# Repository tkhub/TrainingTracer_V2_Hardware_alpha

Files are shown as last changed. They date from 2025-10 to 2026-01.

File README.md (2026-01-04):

[TraningTracer Ver.2](https://rt-net.jp/products/traning-tracer2/)
の勝手改造版です。
tracer

## 改造・改良箇所
* 改造箇所
  * 一般的な3端子レギュレータの端子配置(Vin-GND-Vout)への対応
    * [スーパー3端子レギュレータ](https://akizukidenshi.com/catalog/g/g107178/)が使用でき、高電圧なLiPoバッテリーに対応可能
  * 逆電圧による3端子レギュレータ破壊防止のDiを追加
  * 改造用に各種電源とI2Cのピンアウトを設定
  * ディスコンになったBMX055のかわりにBNO055を搭載可能
    * ショートピンの設定(ハンダ盛り)が必要
  * 自励式ブザーの代わりに圧電スピーカーを搭載可能でより多彩な情報を通知可能
    * 自励式ブザーを使用時は直流阻止コンデンサのC5をショートすること
  * I2Cディスプレイ用コネクタの設定
    * [0.96インチOLEDディスプレイ](https://akizukidenshi.com/catalog/g/g112031/)のような追加ディスプレイによりより多くの情報をユーザーに通知可能
  * 基板上にラインズレ量を測るスケールを追加
  * その他小変更
* 改良箇所
  * パイロットランプの追加
    * 電源入れっぱなしの防止
  * [バッテリー電圧計測のブレ対策にコンデンサC4を追加](https://github.com/rt-net/TrainingTracer_V2_Hardware/issues/1)
  * [回路図上のラベルとセンサの物理配置、ソフトの命名の整合性確保](https://github.com/rt-net/TrainingTracer_V2_Hardware/issues/2)
  * [プログラム書き込み中にモータが回転する問題の解決](https://github.com/rt-net/TrainingTracer_Hardware/issues/7)

## フォルダ構成

* 3d_cad_data
　トレーニングトレーサーの3DCADデータ
  STPファイルとIGSファイルで保存しています。
* 3d_print_parts
　トレーニングトレーサーの3Dプリント部品のデータ
  * TrainingTracer_Motor_Mount.stl
    トレーニングトレーサーのモータマウントの3Dモデルです。
  * TrainingTracerV2_Slider.stl
    トレーニングトレーサーのスライダーの3Dモデルです。
  * TrainingTracerV2_Wheel.stl
    トレーニングトレーサーのホイールの3Dモデルです。
* circuits
　トレーニングトレーサーの回路図とNucleoの追加工マニュアル
  * TrainingTracer
    * KiCadのプロジェクトフォルダ
  * old
    * TrainingTracerV2_circuit_rev1.0.pdf
    トレーニングトレーサーのメイン基板の回路図です。
    * TrainingTracer_marker_circuit.pdf
    トレーニングトレーサーのマーカーセンサ基板の回路図です。
  * TrainingTracer_PCB.pdf
    改造後の基板
  * TrainingTracer_SCH.pdf
    改造後の回路図
  * 出荷時のNucleoの追加工.pdf
    トレーニングトレーサーのNucleoボードに行った追加工の情報です。
    
## 開発について

本リポジトリはオープンソースですが、開発はオープンではありません。  
機能追加については社内のガイドラインを優先します。  
誤植や不具合の修正は常時受け付けています。詳しくは[コントリビューションガイドライン](https://github.com/rt-net/.github/blob/master/CONTRIBUTING.md)に従ってください。

## ライセンス

(C) 2020 RT Corporation \<support@rt-net.jp\>

各ファイルはライセンスがファイル中に明記されている場合、そのライセンスに従います。特に明記されていない場合は、Apache License, Version 2.0に基づき公開されています。  
ライセンスの全文は[LICENSE](./LICENSE)または[https://www.apache.org/licenses/LICENSE-2.0](https://www.apache.org/licenses/LICENSE-2.0)から確認できます。

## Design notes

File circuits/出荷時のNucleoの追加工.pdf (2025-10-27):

© 2020

# トレーニングトレーサーにおける

# Nucleoの追加工

# 本資料について

トレーニングトレーサーへNucleoを搭載するために実施した作業内容を記載していま す。別途Nucleoを購入して搭載したい場合に参照してください。

# 抵抗の加工

安全性と使いやすさを考慮して、単4アルカリ電池直列4個接続で稼働できるよう、 Nucleoに搭載の3.3Vのレギュレータを使わず、外付けのレギュータでマイコン等へ電力を 供給しています。そのため、SB14の0Ω抵抗を外す必要があります。 3.3Vを外部から入れるとST-LINKと繋がっているNRSTがずっとLOWと認識してしまい、 マイコンが起動しないので、SB9も外す必要があります。 また、アナログピンA5、A4がデータピンD5、D4に接続している状態であり、A/DとI2C が同時に使えないため、0Ω抵抗のSB16とSB18を外す必要があります。

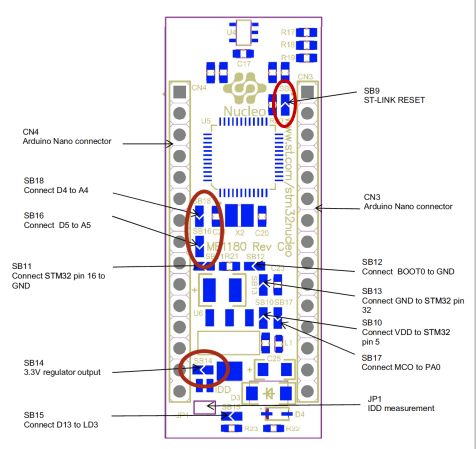
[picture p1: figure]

図.1 Nucleoボードの裏側¹

# マーカセンサについて

Nucleoのパッケージのバージョンが1.8の場合、マーカーセンサに関しては、接続されて いるピンではArduino IDEの関数がそのままでは使えないため、STEP5で機能を追加してあ ります。(パッケージのバージョンが1.9の場合は変更の必要はありません。)また、一部 Nucleoのパッケージを書き換える必要があります。NUCLEO-F303のオリジナルは、A4と D4、A5とD5がボード上で短絡しています。その関係で、A4とA5のピンに関しては、アナ ログ入力で変換できないようにパッケージ側でコメントアウトされています。プログラムを 実行する前に、テキストエディタなどでパッケージ内にある以下のファイルを修正する必要 があります。

## Windowsの場合

C:\Users\ユーザー名\ドキュメント
\ArduinoData\packages\STM32\hardware\stm32\1.8.0\variants\NUCLEO_F303K8/Pe ripheralPins.cの49と50行目のコメントアウト//を解除

## Macの場合

User/ユーザー名
/Library/Arduino15/packages/STM32/hardware/stm32/1.8.0/variants/NUCLEO_F303 K8/PeripheralPins.cの49と50行目のコメントアウト//を解除

## Linuxの場合

/home/ユーザー名
/.arduino15/packages/STM32/hardware/stm32/1.8.0/variants/NUCLEO_F303K8/Peri pheralPins.cの49と50行目のコメントアウト//を解除

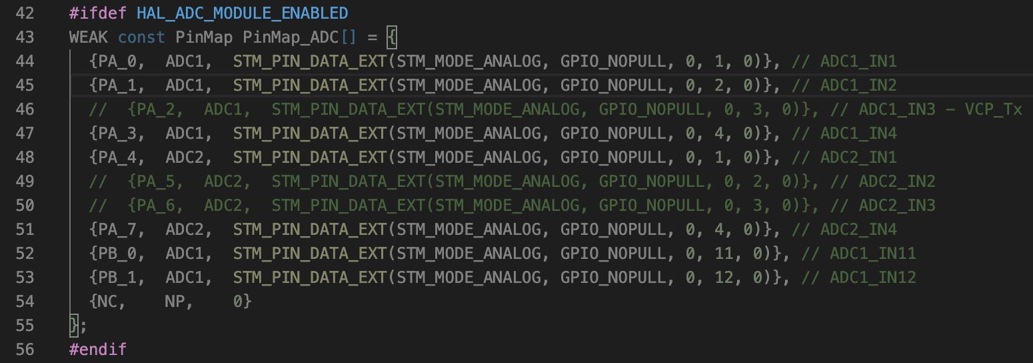
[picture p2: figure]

図.2 修正前のPeripheralPins.c

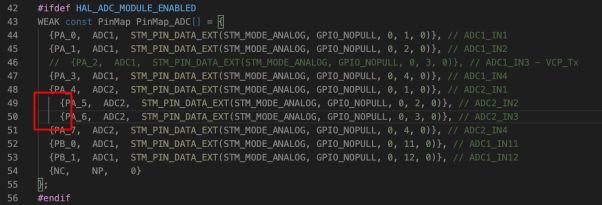
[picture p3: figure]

図.3 修正後のPeripheralPins.c

出典

1. STmicroerectronics社UM1727 User manual Getting started with STM32 Nucleo board software development tools https://www.st.com/resource/en/user_manual/dm00231744-stm32-nucleo32-boardsmb1180-stmicroelectronics.pdf (https://www.st.com/resource/en/user_manual/dm00231744-stm32-nucleo32-boards-mb1180-stmicroelectronics.pdf)

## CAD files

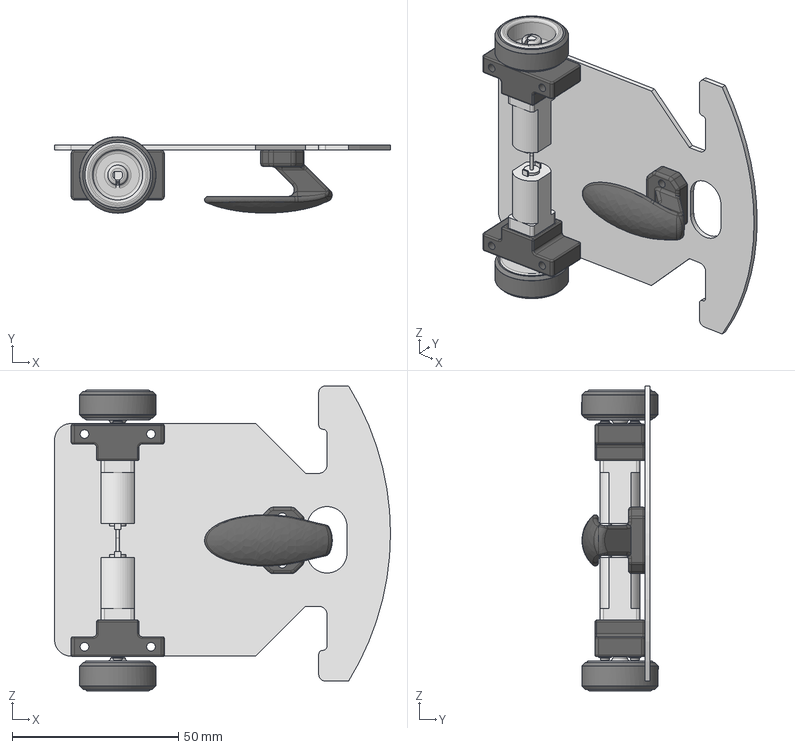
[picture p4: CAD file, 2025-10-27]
3d_cad_data/TrainingTracerV2.step
101.1 x 23.0 x 91.8 mm
MicroMetalGearmotor x 2
TrainingTracerBoard0.1
TrainingTracer_MotorMount_20200427 x 2
M1.6平ワッシャ_FW-1638-03N x 4
小ねじM1.6-4_U-1640-03 x 4
タイヤ(MZW2-20) x 2
TrainingTracer_Slider_20200420

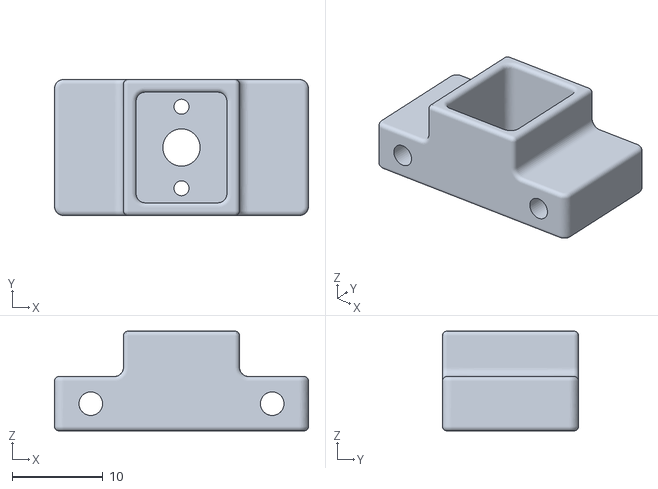
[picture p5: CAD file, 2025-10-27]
3d_print_parts/TrainingTracer_MotorMount.stl
28.0 x 15.0 x 11.0

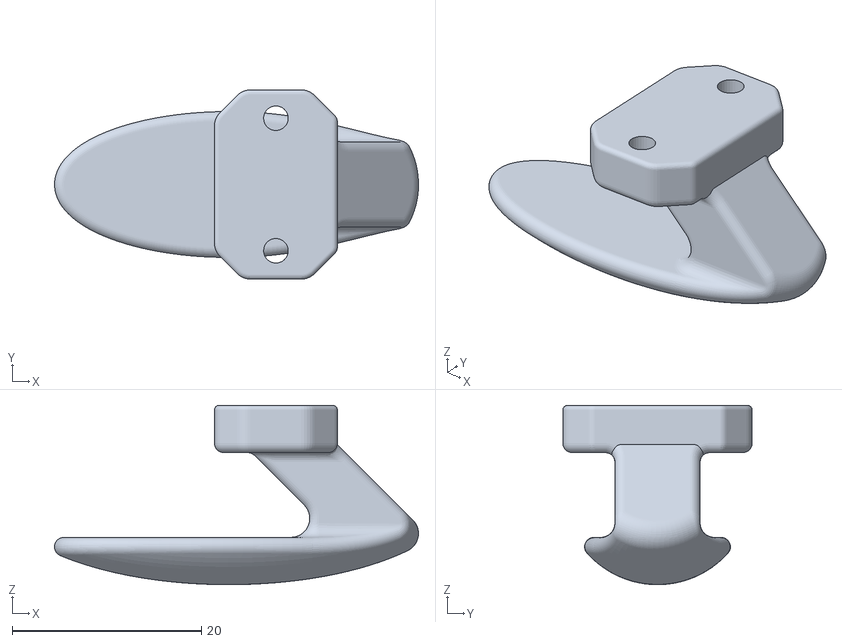
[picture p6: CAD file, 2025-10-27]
3d_print_parts/TrainingTracerV2_Slider.stl
38.4 x 20.0 x 18.9

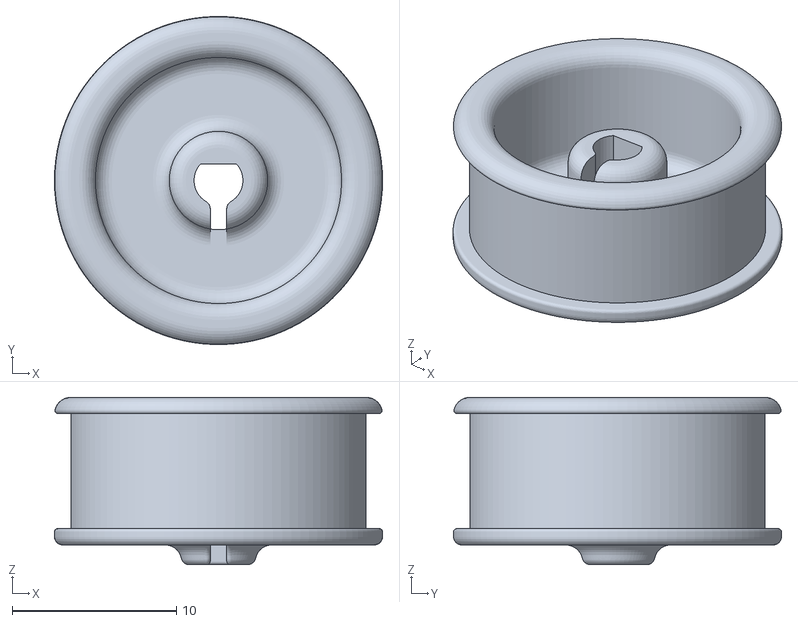
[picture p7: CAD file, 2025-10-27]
3d_print_parts/TrainingTracerV2_Wheel.stl
20.0 x 20.0 x 10.2

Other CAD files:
3d_cad_data/TrainingTracerV2.iges

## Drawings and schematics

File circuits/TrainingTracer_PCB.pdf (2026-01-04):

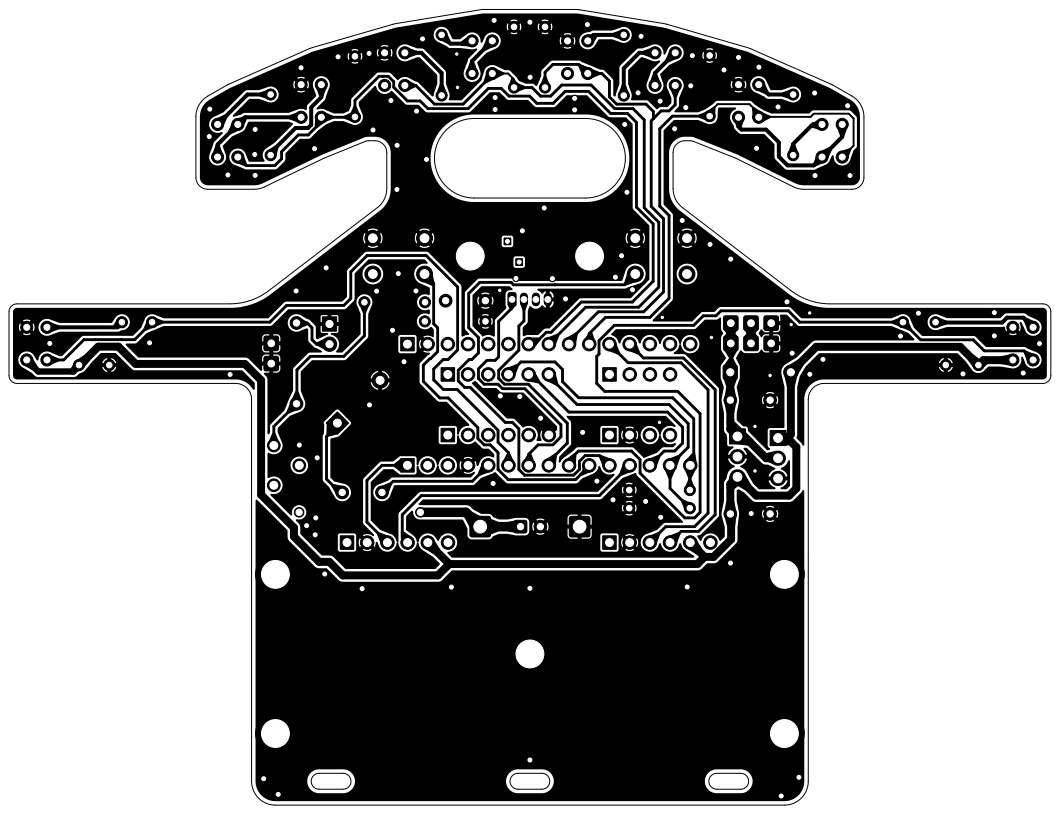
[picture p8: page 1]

Id: 1/4 Title: File: TrainingTracer.kicad_pcb Sheet:

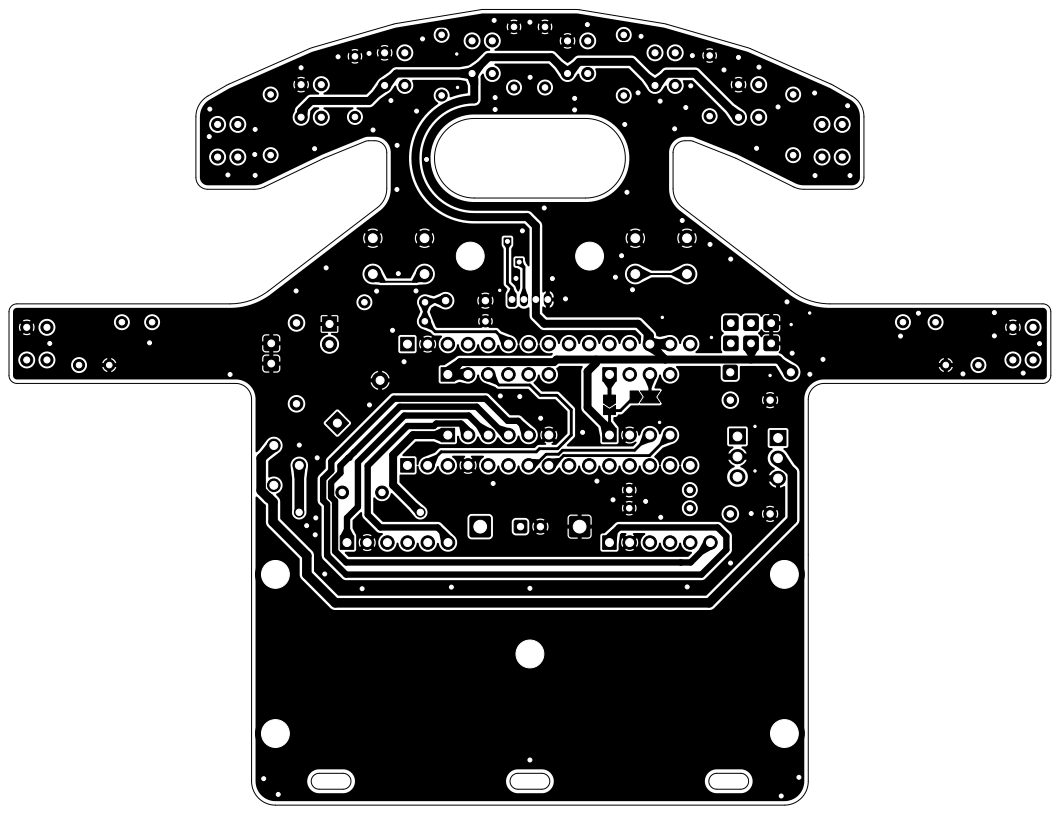
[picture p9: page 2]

Id: 2/4 Title: File: TrainingTracer.kicad_pcb Sheet:

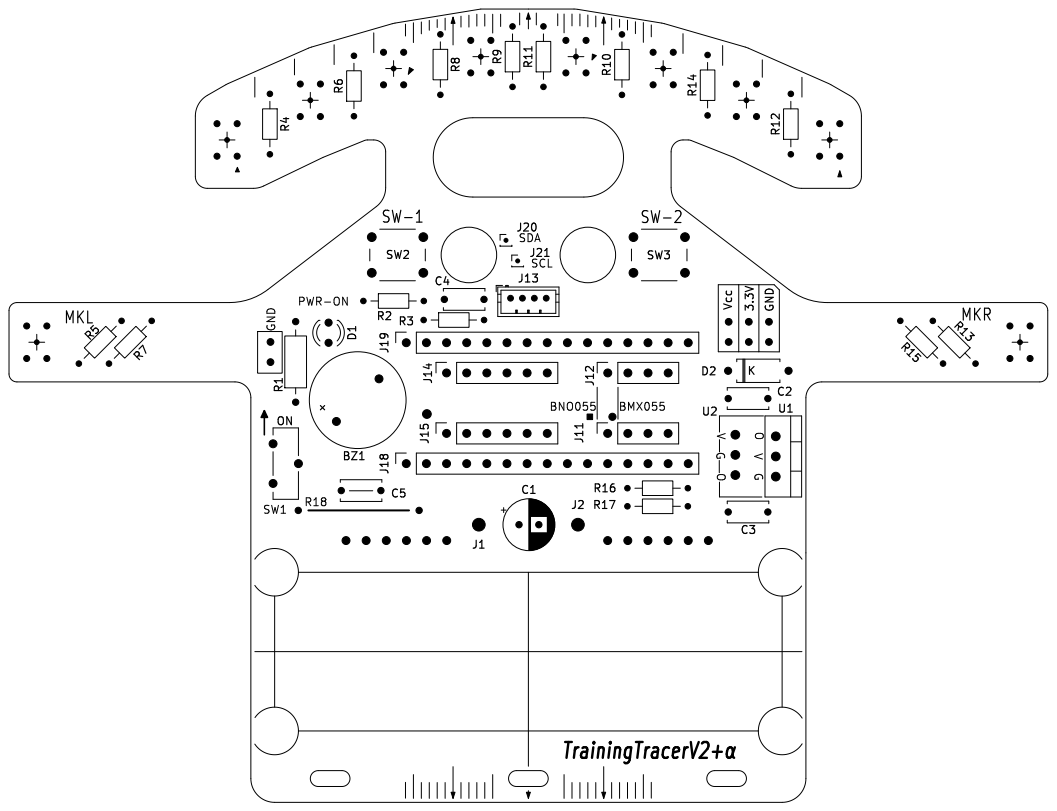
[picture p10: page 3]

Id: 3/4 Title: File: TrainingTracer.kicad_pcb Sheet: þÿTrainingTracerV2+± MKL

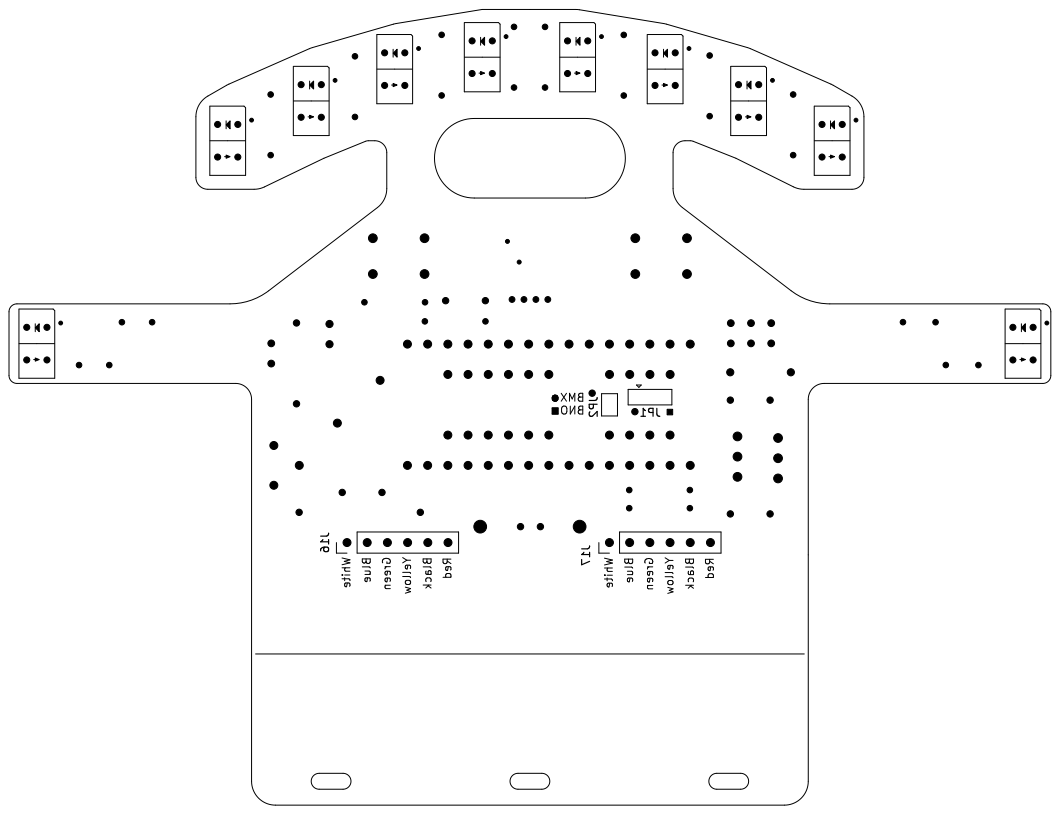
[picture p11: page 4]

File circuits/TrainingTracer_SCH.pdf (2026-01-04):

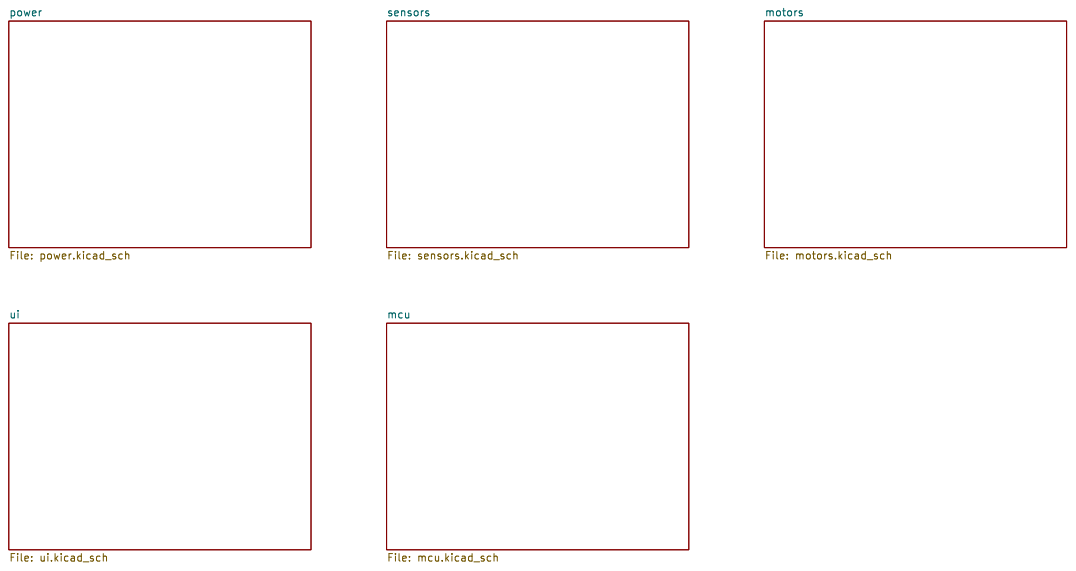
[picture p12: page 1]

Id: 1/6 Title: File: TrainingTracer.kicad_sch Sheet: /

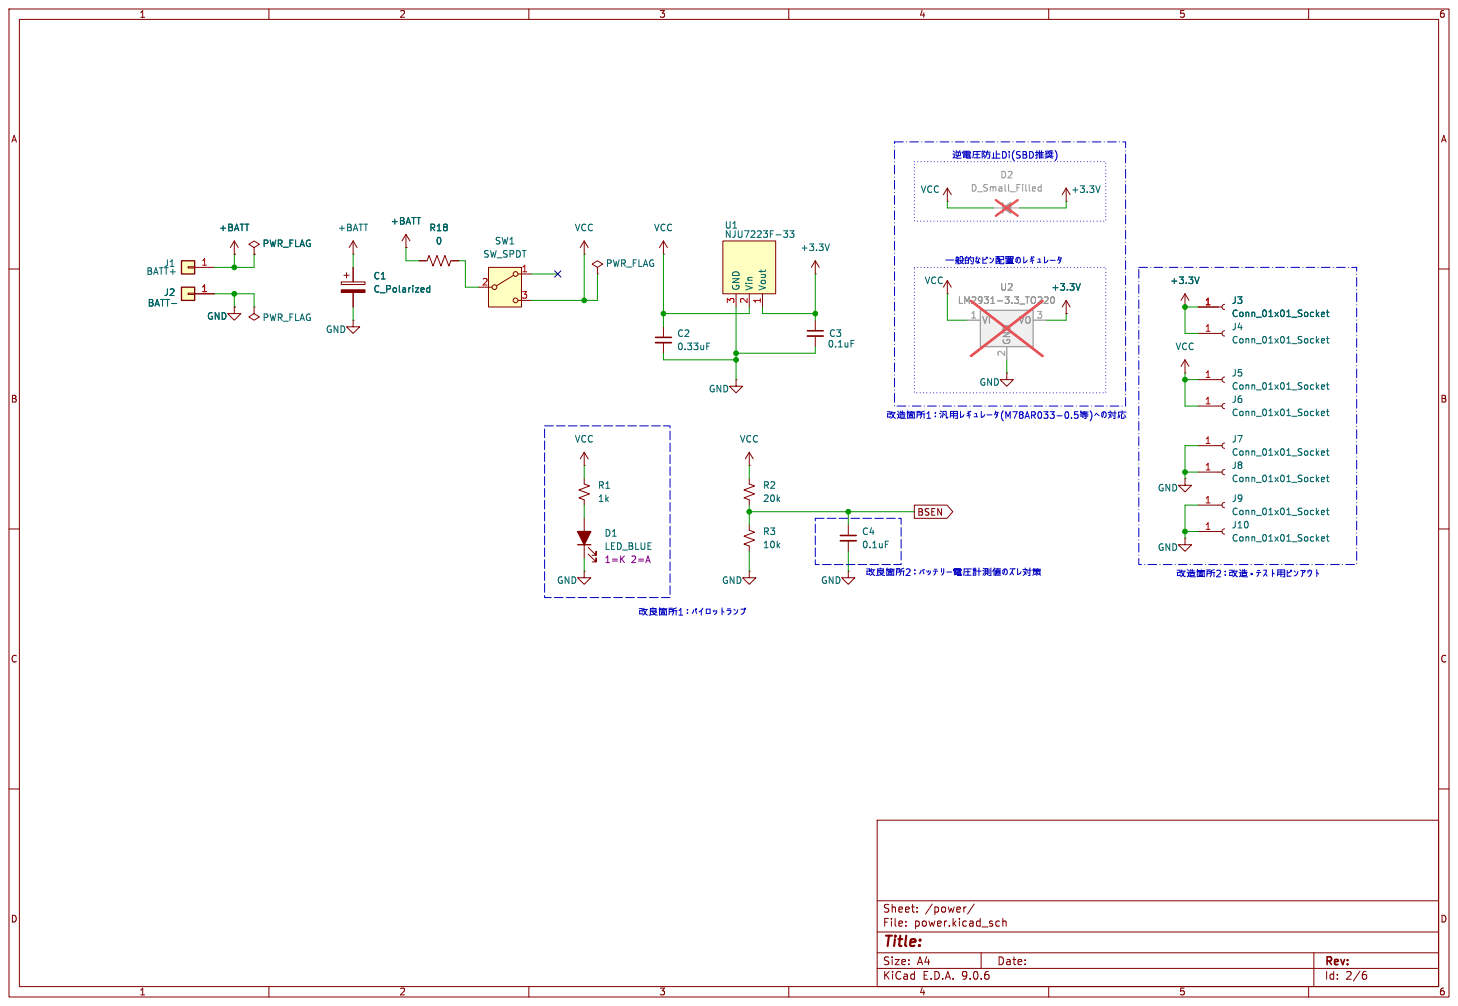
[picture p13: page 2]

20k VCC

Id: 2/6 Title: File: power.kicad_sch Sheet: /power/

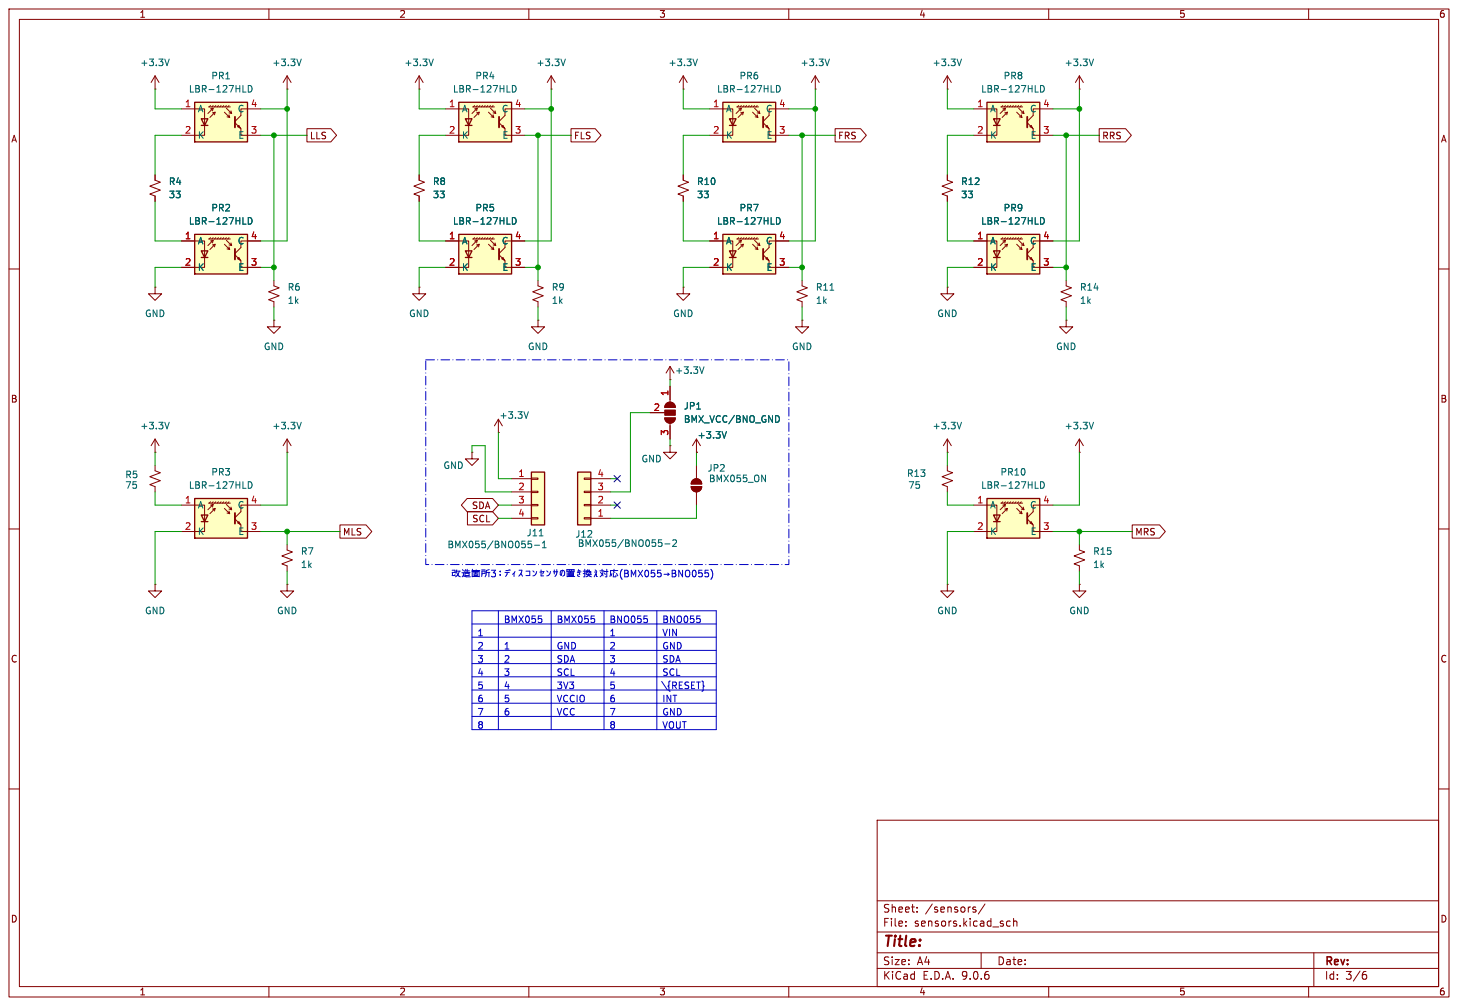
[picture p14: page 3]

Id: 3/6 Title: File: sensors.kicad_sch Sheet: /sensors/

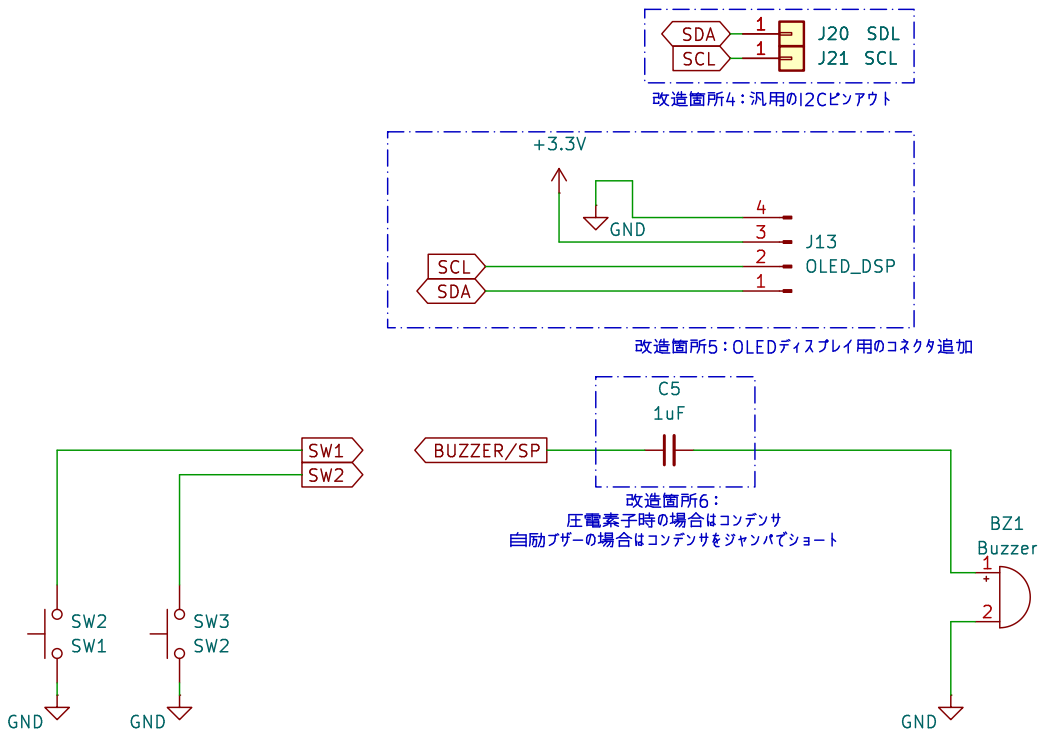
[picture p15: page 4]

Id: 4/6 Title: File: ui.kicad_sch Sheet: /ui/ SW3 SW2

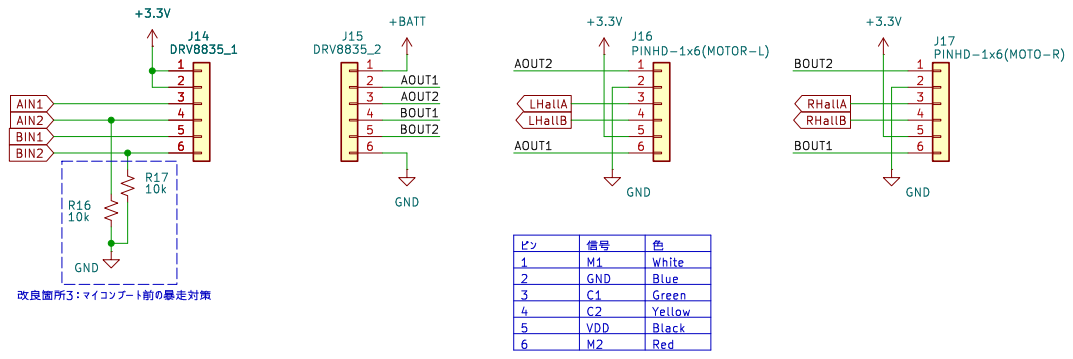
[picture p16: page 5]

þÿ0Ô0ó | þÿOáS÷ M1 | þÿ‚r 1 White

2 | GND | Blue
3 | C1 | Green
4 | C2 | Yellow

Id: 5/6 Title: File: motors.kicad_sch Sheet: /motors/

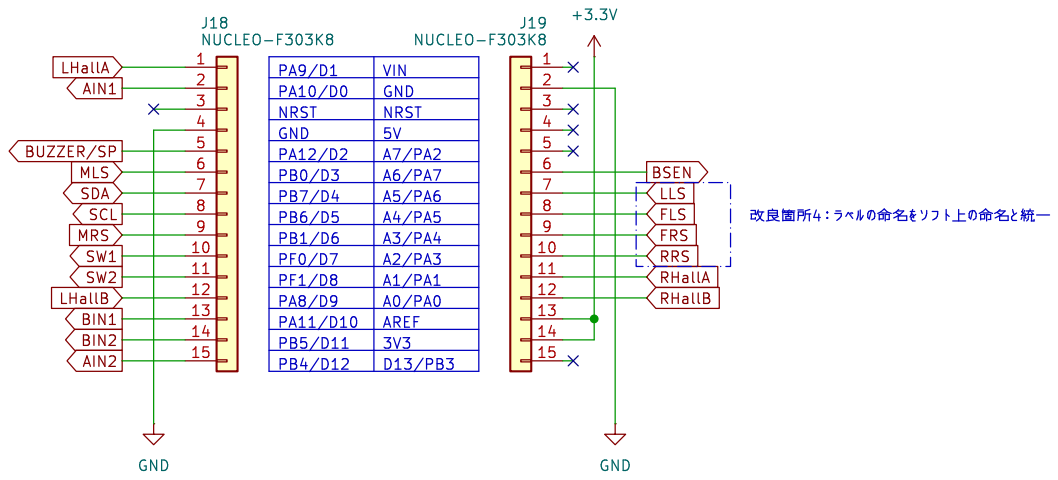
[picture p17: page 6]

PA9/D1 | VIN
PA10/D0 | GND
NRST | NRST GND 5V

PA12/D2 | A7/PA2 PB0/D3 A6/PA7 PB7/D4 A5/PA6 PB6/D5 A4/PA5 PB1/D6 A3/PA4 PF0/D7 A2/PA3 PF1/D8 A1/PA1 PA8/D9 A0/PA0 PA11/D10 AREF PB5/D11 3V3 PB4/D12 D13/PB3

10
11
12
13

Id: 6/6 Title: File: mcu.kicad_sch Sheet: /mcu/ GND

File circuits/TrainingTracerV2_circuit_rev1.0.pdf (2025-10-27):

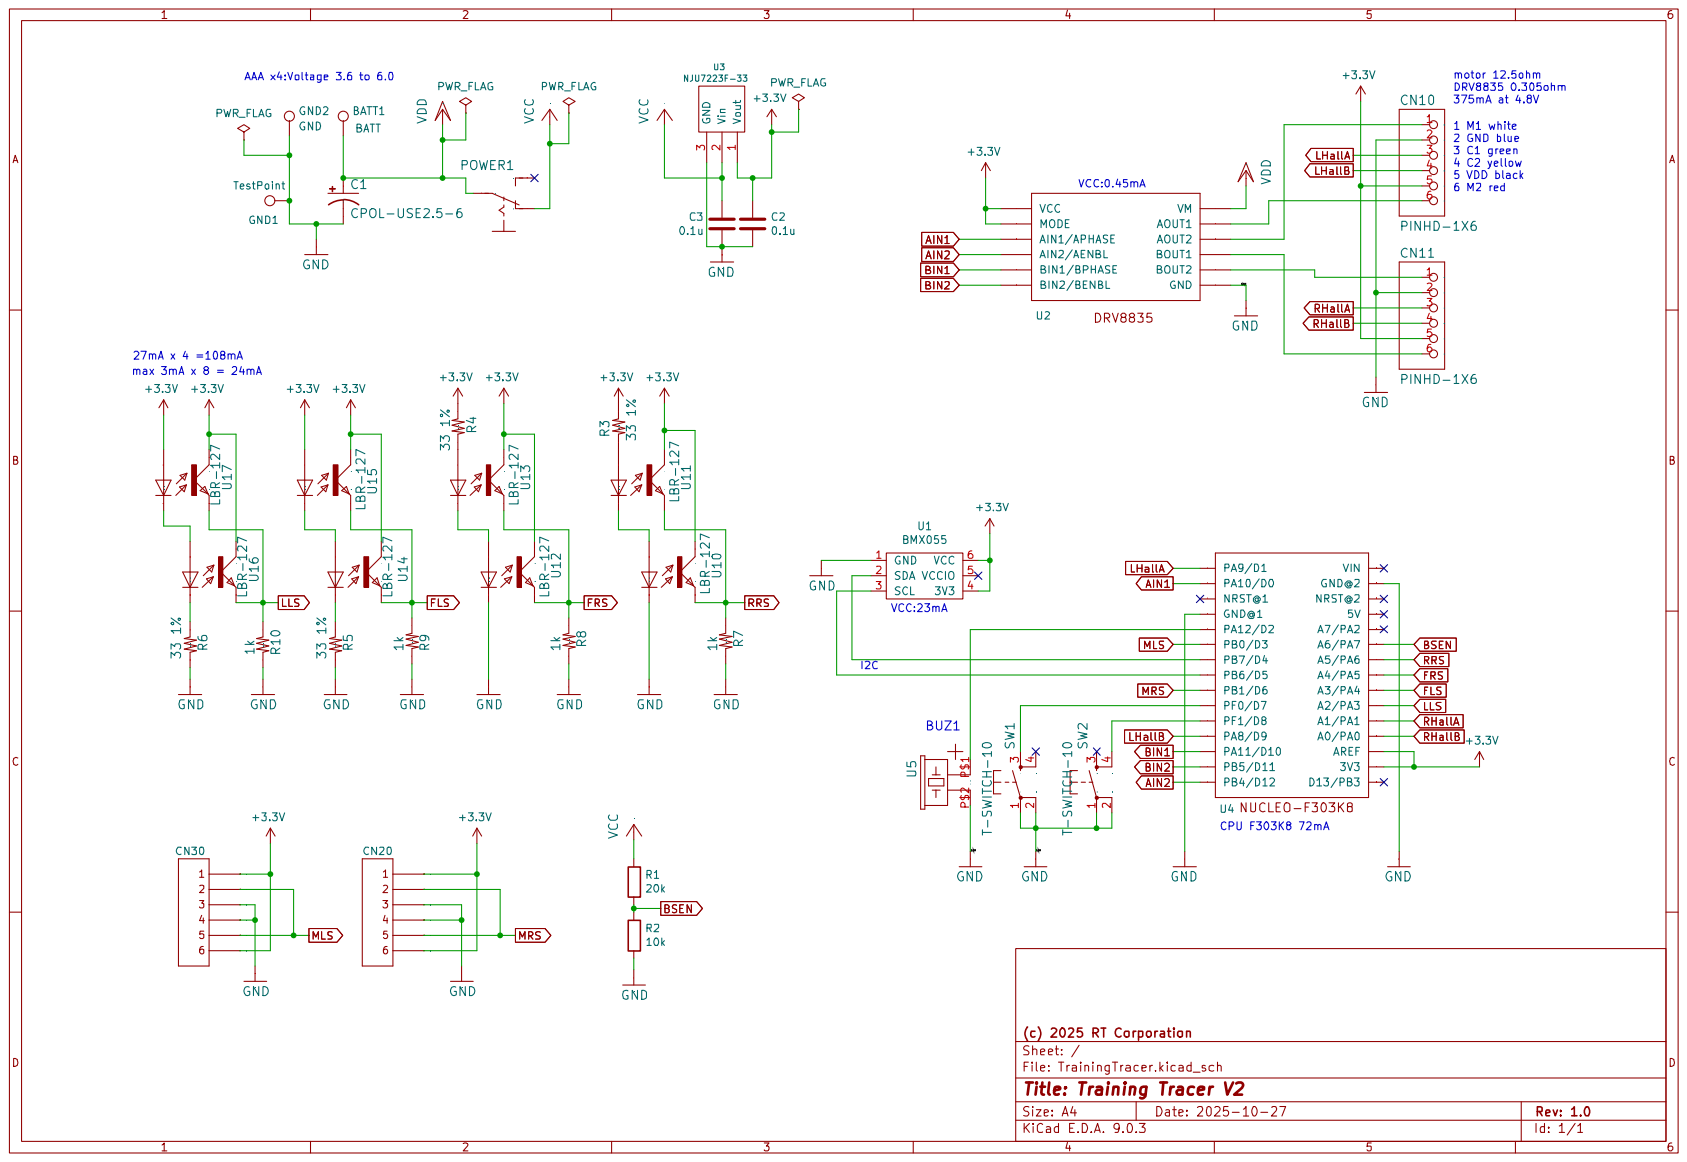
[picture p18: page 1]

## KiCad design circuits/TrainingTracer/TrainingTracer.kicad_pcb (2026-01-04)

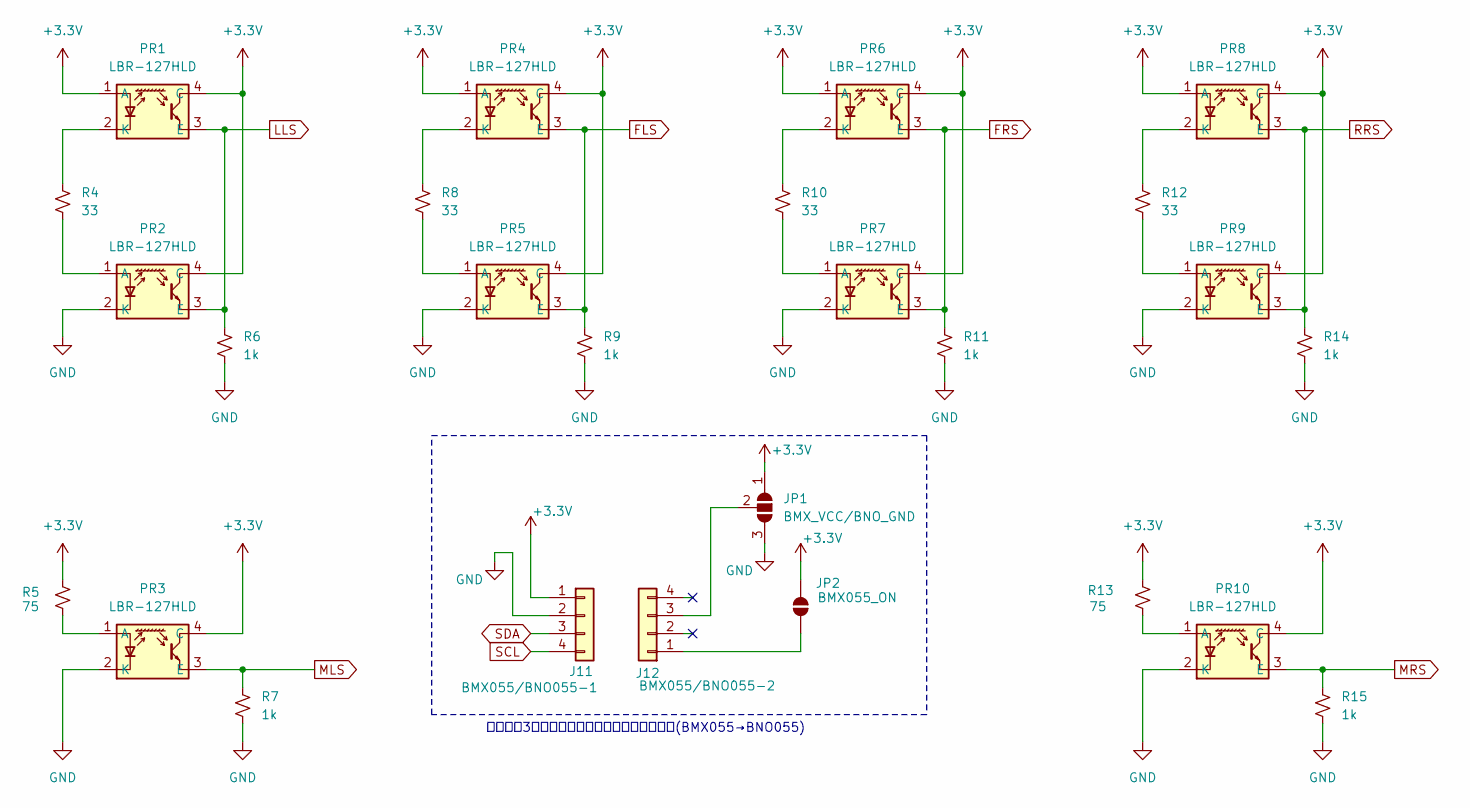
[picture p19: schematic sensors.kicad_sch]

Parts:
J11: BMX055/BNO055-1; PinSocket_1x04_P2.54mm_Vertical
J12: BMX055/BNO055-2; PinSocket_1x04_P2.54mm_Vertical
JP1: BMX_VCC/BNO_GND; SolderJumper-3_P2.0mm_Open_TrianglePad1.0x1.5mm
JP2: BMX055_ON; SolderJumper-2_P1.3mm_Open_TrianglePad1.0x1.5mm
PR1, PR2, PR3, PR4, PR5, PR6, PR7, PR8, PR9, PR10: LBR-127HLD; LED-AK_PTR_CE_p410xp254
R4, R8, R10, R12: 33; R_Axial_DIN0204_L3.6mm_D1.6mm_P7.62mm_Horizontal
R5, R13: 75; R_Axial_DIN0204_L3.6mm_D1.6mm_P7.62mm_Horizontal
R6, R7, R9, R11, R14, R15: 1k; R_Axial_DIN0204_L3.6mm_D1.6mm_P7.62mm_Horizontal

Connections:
+3.3V: J11.1, JP1.1 (A), JP2.2 (B), PR1.1 (A), PR1.4 (C), PR2.4 (C), PR3.4 (C), PR4.1 (A), PR4.4 (C), PR5.4 (C), PR6.1 (A), PR6.4 (C), PR7.4 (C), PR8.1 (A), PR8.4 (C), PR9.4 (C), PR10.4 (C), R5.1, R13.1; also elsewhere on the board
FLS: PR4.3 (E), PR5.3 (E), R9.1; also elsewhere on the board
FRS: PR6.3 (E), PR7.3 (E), R11.1; also elsewhere on the board
GND: J11.2, JP1.3 (B), PR2.2 (K), PR3.2 (K), PR5.2 (K), PR7.2 (K), PR9.2 (K), PR10.2 (K), R6.2, R7.2, R9.2, R11.2, R14.2, R15.2; also elsewhere on the board
LLS: PR1.3 (E), PR2.3 (E), R6.1; also elsewhere on the board
MLS: PR3.3 (E), R7.1; also elsewhere on the board
MRS: PR10.3 (E), R15.1; also elsewhere on the board
unnamed: J12.1, JP2.1 (A)
unnamed: J12.3, JP1.2 (C)
unnamed: PR1.2 (K), R4.1
unnamed: PR2.1 (A), R4.2
unnamed: PR3.1 (A), R5.2
unnamed: PR4.2 (K), R8.1
unnamed: PR5.1 (A), R8.2
unnamed: PR6.2 (K), R10.1
unnamed: PR7.1 (A), R10.2
unnamed: PR8.2 (K), R12.1
unnamed: PR9.1 (A), R12.2
unnamed: PR10.1 (A), R13.2
RRS: PR8.3 (E), PR9.3 (E), R14.1; also elsewhere on the board
SCL: J11.4; also elsewhere on the board
SDA: J11.3; also elsewhere on the board

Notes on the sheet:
改造箇所3：ディスコンセンサの置き換え対応(BMX055→BNO055)

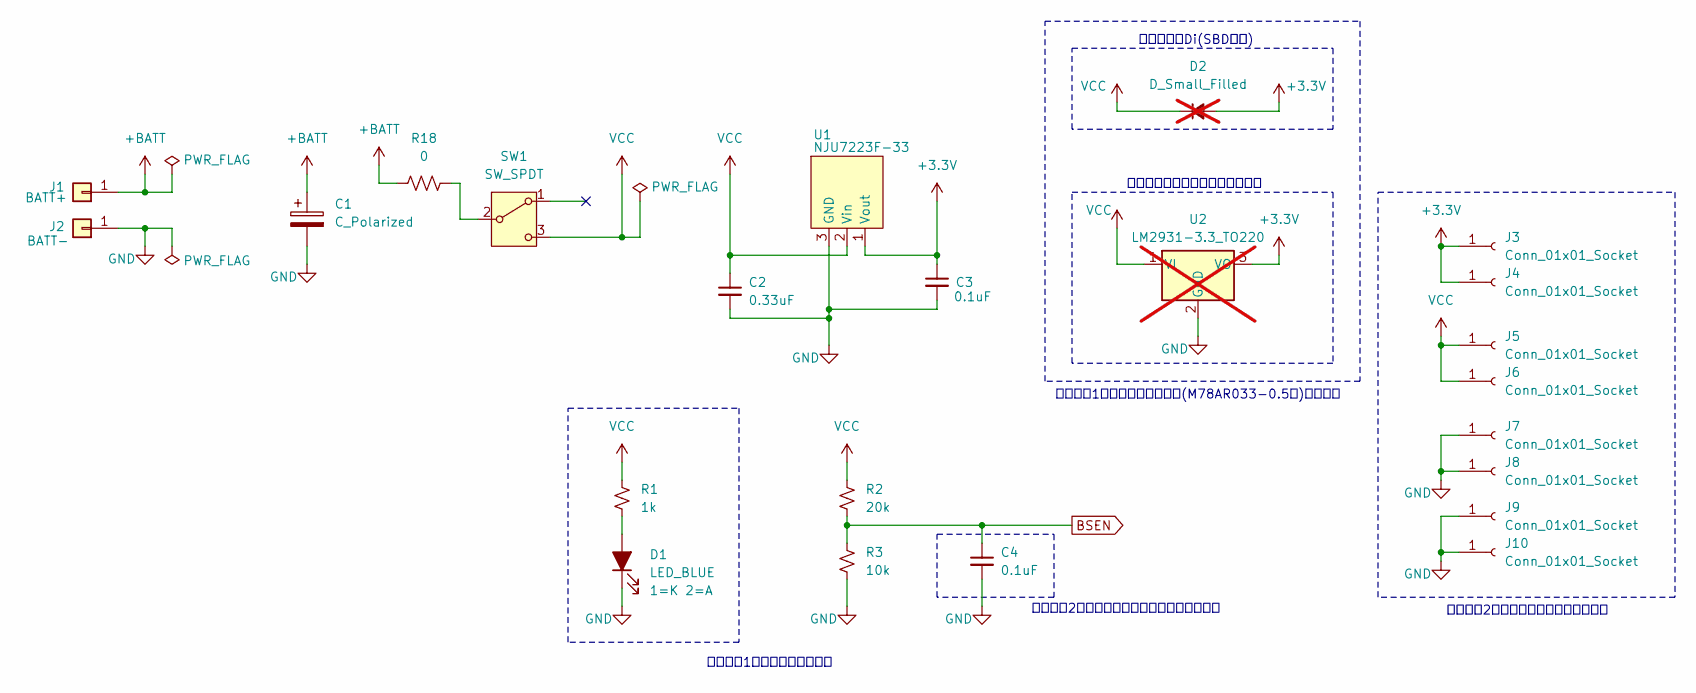
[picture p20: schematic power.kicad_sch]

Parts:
C1: C_Polarized; CP_Radial_D6.3mm_P2.50mm
C2: 0.33uF; C_Disc_D5.0mm_W2.5mm_P5.00mm
C3, C4: 0.1uF; C_Disc_D5.0mm_W2.5mm_P5.00mm
D1: LED_BLUE; LED_D3.0mm
D2: D_Small_Filled; D_A-405_P7.62mm_Horizontal; not fitted
J1: BATT+; SolderWire-0.75sqmm_1x01_D1.25mm_OD2.3mm
J2: BATT-; SolderWire-0.75sqmm_1x01_D1.25mm_OD2.3mm
J3, J4, J5, J6, J7, J8, J9, J10: Conn_01x01_Socket; SolderWire-0.25sqmm_1x01_D0.65mm_OD1.7mm
R1: 1k; R_Axial_DIN0207_L6.3mm_D2.5mm_P10.16mm_Horizontal
R2: 20k; R_Axial_DIN0204_L3.6mm_D1.6mm_P7.62mm_Horizontal
R3: 10k; R_Axial_DIN0204_L3.6mm_D1.6mm_P7.62mm_Horizontal
R18: 0; jmp_15.24mm
SW1: SW_SPDT; Switch
U1: NJU7223F-33; TO-220-3_Vertical
U2: LM2931-3.3_TO220; TO-220-3_Vertical; not fitted

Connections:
+3.3V: C3.1, D2.2 (A), J3.1, J4.1, U1.1 (Vout), U2.3 (VO); also elsewhere on the board
+BATT: C1.1, J1.1, R18.1; also elsewhere on the board
BSEN: C4.1, R2.2, R3.1; also elsewhere on the board
GND: C1.2, C2.2, C3.2, C4.2, D1.1 (K), J2.1, J7.1, J8.1, J9.1, J10.1, R3.2, U1.3 (GND), U2.2 (GND); also elsewhere on the board
unnamed: D1.2 (A), R1.2
unnamed: R18.2, SW1.2 (B)
VCC: C2.1, D2.1 (K), J5.1, J6.1, R1.1, R2.1, SW1.3 (C), U1.2 (Vin), U2.1 (VI)

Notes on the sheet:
改造箇所1：汎用レギュレータ(M78AR033-0.5等)への対応
逆電圧防止Di(SBD推奨)
改良箇所1：パイロットランプ
改造箇所2：改造・テスト用ピンアウト
改良箇所2：バッテリー電圧計測値のズレ対策
一般的なピン配置のレギュレータ

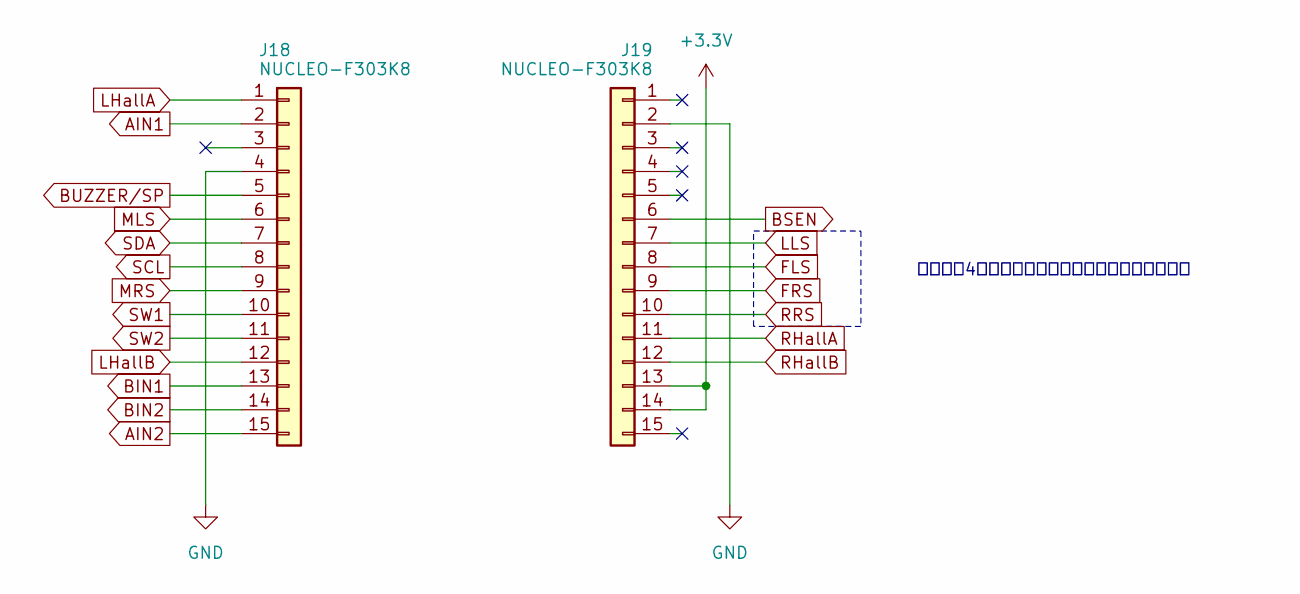
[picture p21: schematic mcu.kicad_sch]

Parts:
J18, J19: NUCLEO-F303K8; PinSocket_1x15_P2.54mm_Vertical

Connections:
+3.3V: J19.13, J19.14; also elsewhere on the board
AIN1: J18.2; also elsewhere on the board
AIN2: J18.15; also elsewhere on the board
BIN1: J18.13; also elsewhere on the board
BIN2: J18.14; also elsewhere on the board
BSEN: J19.6; also elsewhere on the board
BUZZER/SP: J18.5; also elsewhere on the board
FLS: J19.8; also elsewhere on the board
FRS: J19.9; also elsewhere on the board
GND: J18.4, J19.2; also elsewhere on the board
LHallA: J18.1; also elsewhere on the board
LHallB: J18.12; also elsewhere on the board
LLS: J19.7; also elsewhere on the board
MLS: J18.6; also elsewhere on the board
MRS: J18.9; also elsewhere on the board
RHallA: J19.11; also elsewhere on the board
RHallB: J19.12; also elsewhere on the board
RRS: J19.10; also elsewhere on the board
SCL: J18.8; also elsewhere on the board
SDA: J18.7; also elsewhere on the board
SW1: J18.10; also elsewhere on the board
SW2: J18.11; also elsewhere on the board

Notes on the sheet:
改良箇所4：ラベルの命名をソフト上の命名と統一

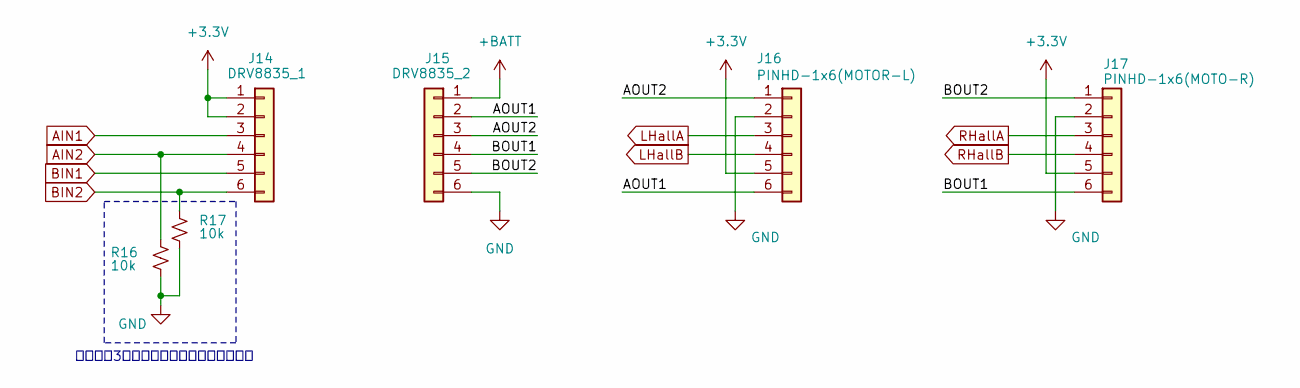
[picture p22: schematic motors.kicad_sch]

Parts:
J14: DRV8835_1; PinSocket_1x06_P2.54mm_Vertical
J15: DRV8835_2; PinSocket_1x06_P2.54mm_Vertical
J16: PINHD-1x6(MOTOR-L); PinSocket_1x06_P2.54mm_Vertical
J17: PINHD-1x6(MOTO-R); PinSocket_1x06_P2.54mm_Vertical
R16, R17: 10k; R_Axial_DIN0204_L3.6mm_D1.6mm_P7.62mm_Horizontal

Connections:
+3.3V: J14.1, J14.2, J16.5, J17.5; also elsewhere on the board
+BATT: J15.1; also elsewhere on the board
/motors/AOUT1: J15.2, J16.6
/motors/AOUT2: J15.3, J16.1
/motors/BOUT1: J15.4, J17.6
/motors/BOUT2: J15.5, J17.1
AIN1: J14.3; also elsewhere on the board
AIN2: J14.4, R16.1; also elsewhere on the board
BIN1: J14.5; also elsewhere on the board
BIN2: J14.6, R17.1; also elsewhere on the board
GND: J15.6, J16.2, J17.2, R16.2, R17.2; also elsewhere on the board
LHallA: J16.3; also elsewhere on the board
LHallB: J16.4; also elsewhere on the board
RHallA: J17.3; also elsewhere on the board
RHallB: J17.4; also elsewhere on the board

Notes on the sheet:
改良箇所3：マイコンブート前の暴走対策

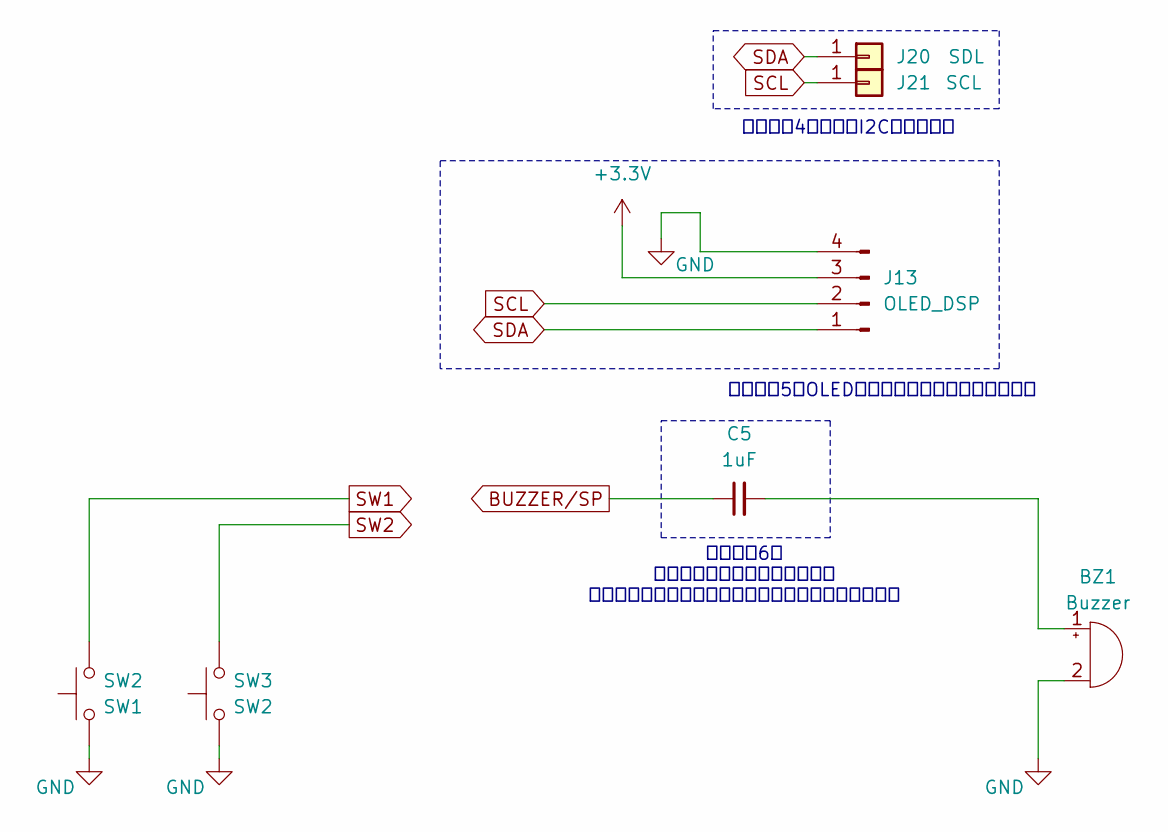
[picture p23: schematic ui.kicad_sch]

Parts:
BZ1: Buzzer; Buzzer_12x9.5RM7.6
C5: 1uF; C_Disc_D5.0mm_W2.5mm_P5.00mm
J13: OLED_DSP; JST_ZH_B4B-ZR_1x04_P1.50mm_Vertical
J20: SDL; PinHeader_1x01_P1.00mm_Vertical
J21: SCL; PinHeader_1x01_P1.00mm_Vertical
SW2: SW1; SW_PUSH_6mm_H7.3mm
SW3: SW2; SW_PUSH_6mm_H7.3mm

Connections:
+3.3V: J13.3; also elsewhere on the board
BUZZER/SP: C5.1; also elsewhere on the board
GND: BZ1.2 (-), J13.4, SW2.1, SW3.1; also elsewhere on the board
unnamed: BZ1.1 (+), C5.2
SCL: J13.2, J21.1; also elsewhere on the board
SDA: J13.1, J20.1; also elsewhere on the board
SW1: SW2.2; also elsewhere on the board
SW2: SW3.2; also elsewhere on the board

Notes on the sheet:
改造箇所6： 圧電素子時の場合はコンデンサ 自励ブザーの場合はコンデンサをジャンパでショート
改造箇所5：OLEDディスプレイ用のコネクタ追加
改造箇所4：汎用のI2Cピンアウト

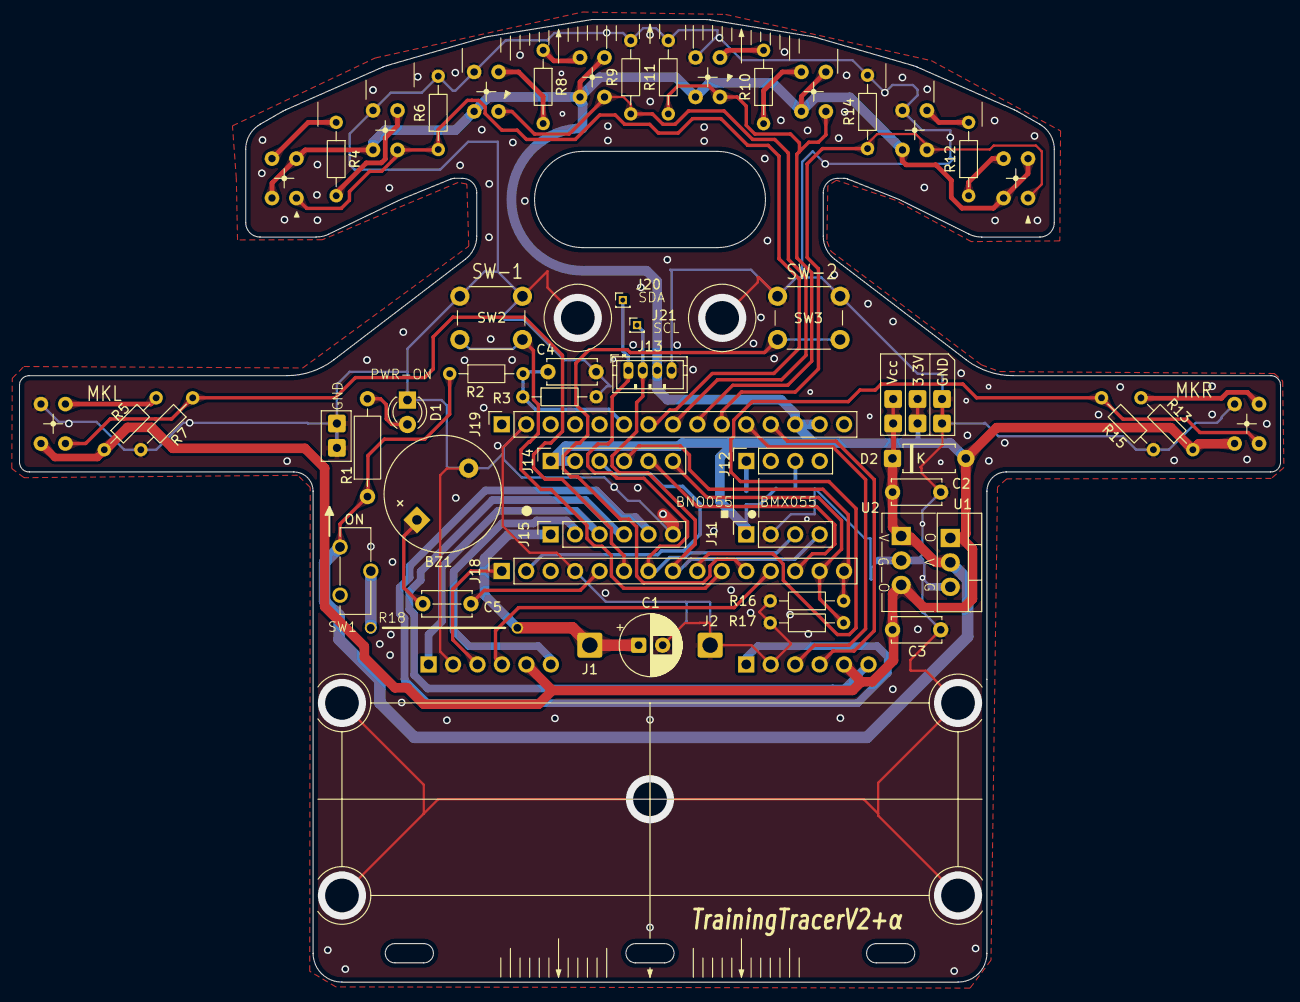
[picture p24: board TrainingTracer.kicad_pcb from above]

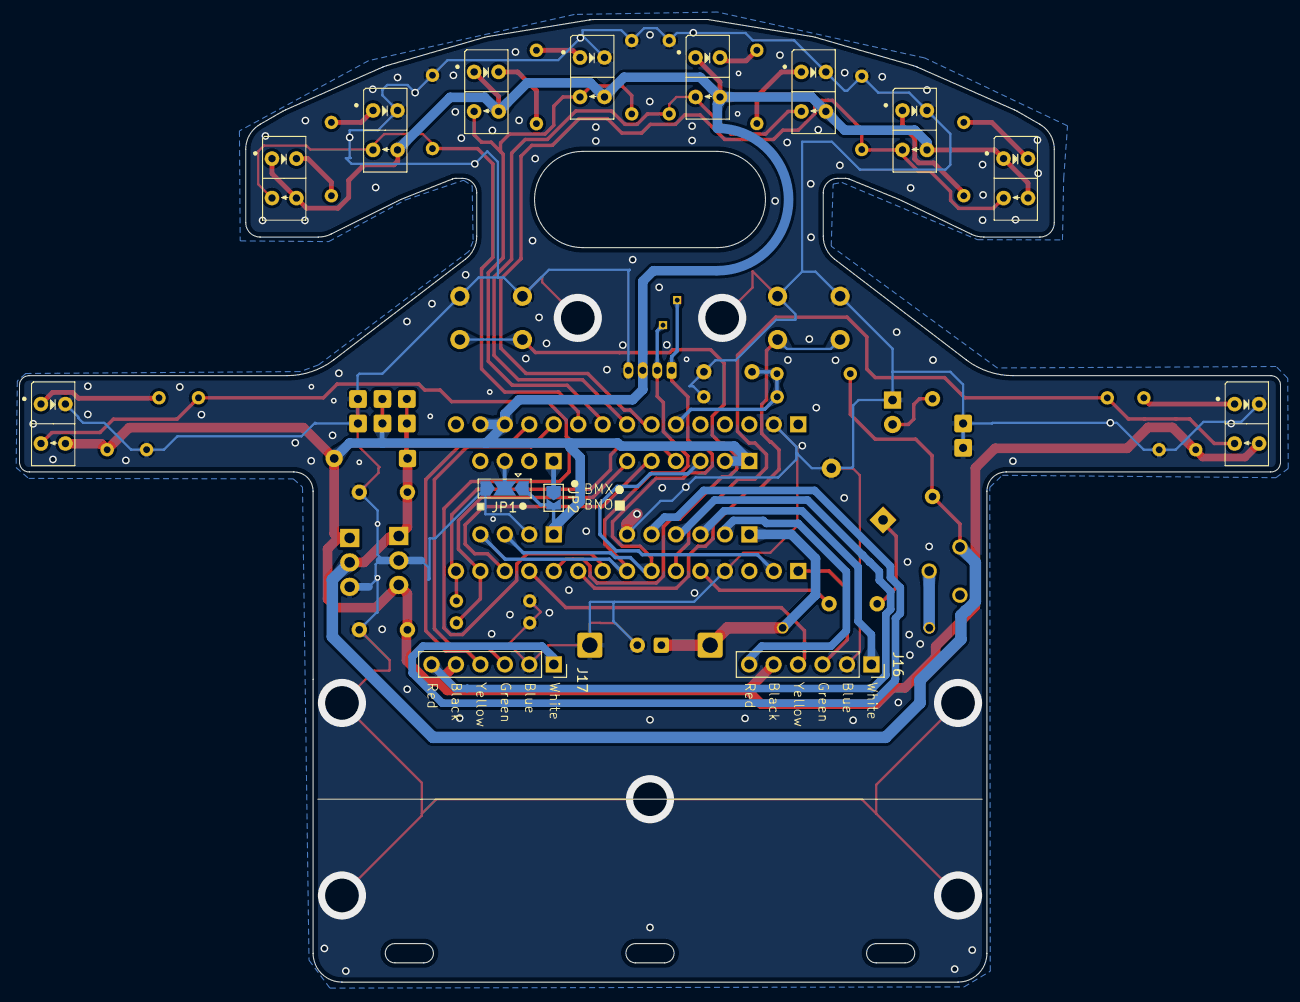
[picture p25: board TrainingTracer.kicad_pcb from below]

Board: 2 copper layers, 131.0 x 100.0 mm, 64 parts (14 on the bottom side), 43 nets.

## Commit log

2025-12-29 回路作成
    [TrainingTracer.kicad_pcb, TrainingTracer.kicad_sch, mcu.kicad_sch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]
2026-01-03 回路完成
    [TrainingTracer.kicad_pcb, mcu.kicad_sch, motors.kicad_sch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]
2026-01-03 回路図のPDF出力
2026-01-03 PCBのPDF出力
    [TrainingTracer.kicad_pcb, motors.kicad_sch, power.kicad_sch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]
2026-01-04 ゴミファイル削除。PDFの移動。
    [TrainingTracer.kicad_pcb]
2026-01-04 バックアップファイル追跡の解除
2026-01-04 gitignore編集
2026-01-04 Update README with hardware modification details
    改造・改良箇所の明記
2026-01-04 改造箇所の漏れを追加 (+その他)
    [TrainingTracer.kicad_pcb, mcu.kicad_sch, ui.kicad_sch]
2026-01-04 PCB後進
    [TrainingTracer.kicad_pcb]
